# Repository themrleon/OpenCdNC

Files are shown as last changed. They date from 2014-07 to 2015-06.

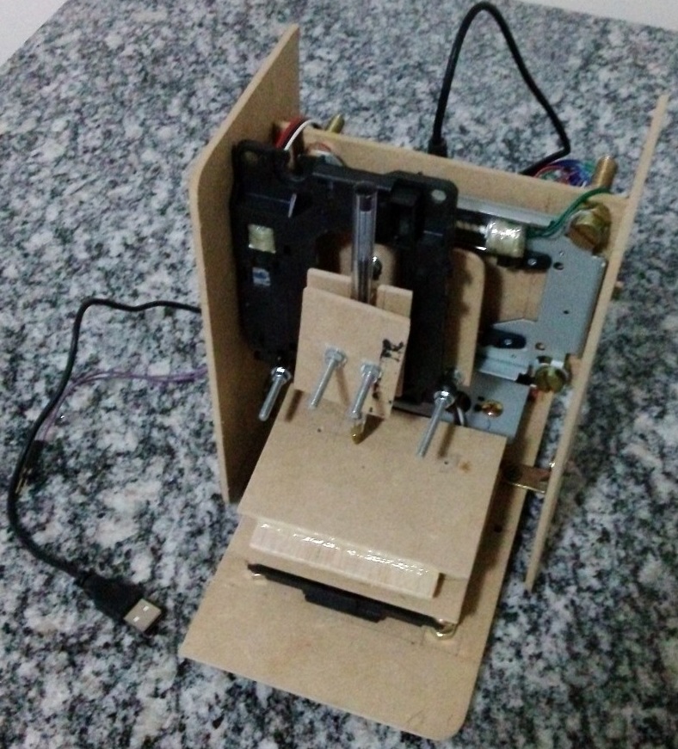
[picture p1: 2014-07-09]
Photos/full_off.jpg

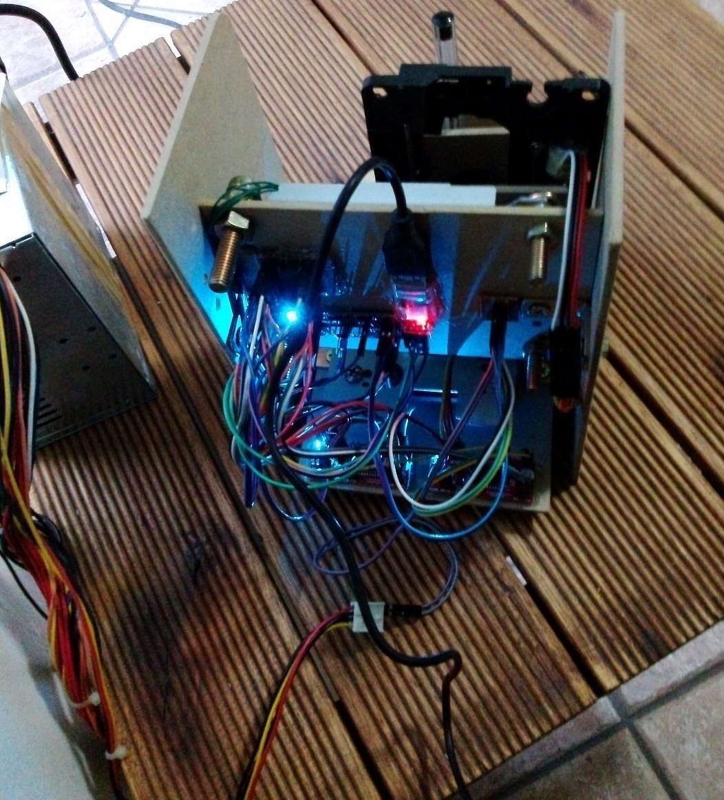
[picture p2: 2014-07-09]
Photos/back_on.jpg

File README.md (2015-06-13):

# OpenCdNC
<div align="justify">I always wanted a fast way to make PCB prototype before send the project to a fabhouse and wait 2 or more months to see the result. This is why I built this CNC, it's made from cd-rom parts and was inspired viewing some similar projects on internet.</div>

(https://www.youtube.com/watch?v=3wD8tHKAZS0)
(https://www.youtube.com/watch?v=hrWGD7YXcFc)

## Articles
* http://www.l3oc.com/2015/06/opencdnc-cnc-made-from-cdrom-parts.html
* http://hackaday.com/2014/07/09/cd-drive-cnc-machine-steals-matt-groenings-job-says-ha-ha/
* http://hackedgadgets.com/2014/07/15/opencdnc-cnc-project-made-from-cd-rom-drives/
* http://dangerousprototypes.com/2014/07/17/opencdnc-cnc-project-made-from-cd-rom-drives/
* http://www.geekweek.pl/aktualnosci/19815/maszyna-cnc-ze-starych-napedow-cd

## Features
* Cheap   - Just three cd-rom drives, wood, screws/bolts, cheap electronics, wires and any pen
* Compact - 20x15 cm of size and 35x38 mm of work area (varies from cd-rom), great for home use, small projects and SMDs
* Functional - Print over paper/copper to do circuit boards or just print images
* USB     - Native Windows/Linux USB driver support, no serial/parallel port or drivers needed
* Easy    - Just connect the USB cable to PC and supply the step motor driver with +5 VDC and GND
* Eagle   - Support one of the most popular PCB software design Cadsoft Eagle PCB (with limitations)
* Gerber  - Support GERBER RS274X protocol (with limitations)
* Precise - 0.147 mm virtual precision (varies from cd-rom motors, step motor driver, frame build quality...) 
* Code    - Small, clean and simple code. You can easily change/adapt to your own project

## What is used?
### Hardware
* 1x Microchip PIC16F628A
* 3x Easy Driver v4.4 Step Motor Driver
* 1x PL2303HX USB-Serial TTL Converter
* 3x CD-ROM Drives
* Some wood/screws for frame and wires for electronics

### Software
* Microsoft Windows 7
* Bloodshed Dev-C++ 4.9.9.2
* Microchip MPlab 8.92
* Hitech PICC Lite compiler
* Cadsoft Eagle PCB 6.6.0
* Microsoft Paint

## How the whole thing works?
### Protocol
`x00000y00000z1` - This is all what the firmware understand and need! Just send the X and Y coordinate in 'micrometer' unit and '1' or '2' for Z axis, where 1 = down and 2 = up.

### Software
<div align="justify">The software connect to CNC through a serial connection of 9600 kbps, send commands and wait the CNC process (move the motors), when done, CNC will return back a flag to software (an ASCII '*'), and then the software can send the next command.</div>

### Eagle
<div align="justify">The software was built to work with files generated by eagle CAM processor using the 'GERBER_RS274X' as device. The limitation here is in the gerber rs274x protocol, I added support just to 'wire' tool of Eagle toolbox, that generate these type of gerber commands:</div>
```
X000100Y000100D02*
X000100Y013874D01*
X013874Y013874D01*
X013081Y013908D02*
```
And what this mean? To print anything you will need use the 'wire' tool or import an image (see below).

## How to print images
<div align="justify">First step is convert the image to monochrome bitmap, this can be done with Microsoft Paint, you need reduce the image size too (something between 35x35 and 300x300 pixels would be ok, where less pixels = fast print and script draw time, but low quality). Then at Eagle you must use a script that import this bitmap file and draw the image using the 'wire' tool. The default Eagle's script name is 'import_bmp.ulp', but it draw the image with the 'rectangle' tool (that is useless to my software), so I modified it to draw using the 'wire' tool. Details in the tutorial folder.</div>

## License
See [LICENSE](https://github.com/themrleon/OpenCdNC/blob/master/LICENSE)

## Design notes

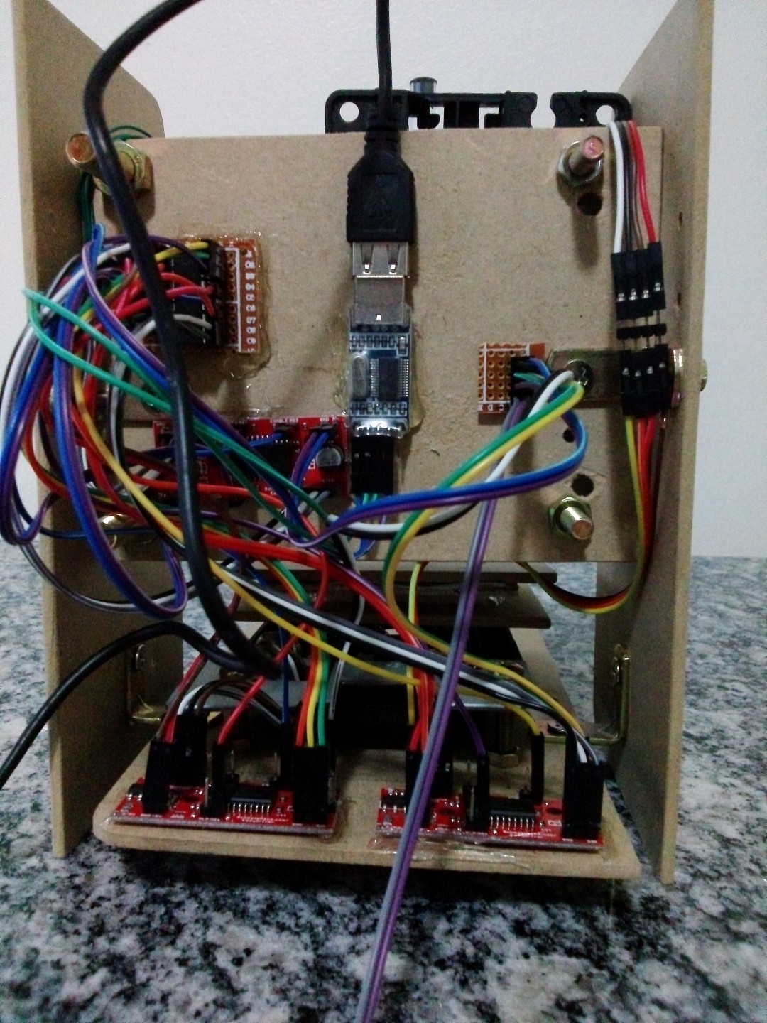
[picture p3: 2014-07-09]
Photos/back_close.jpg

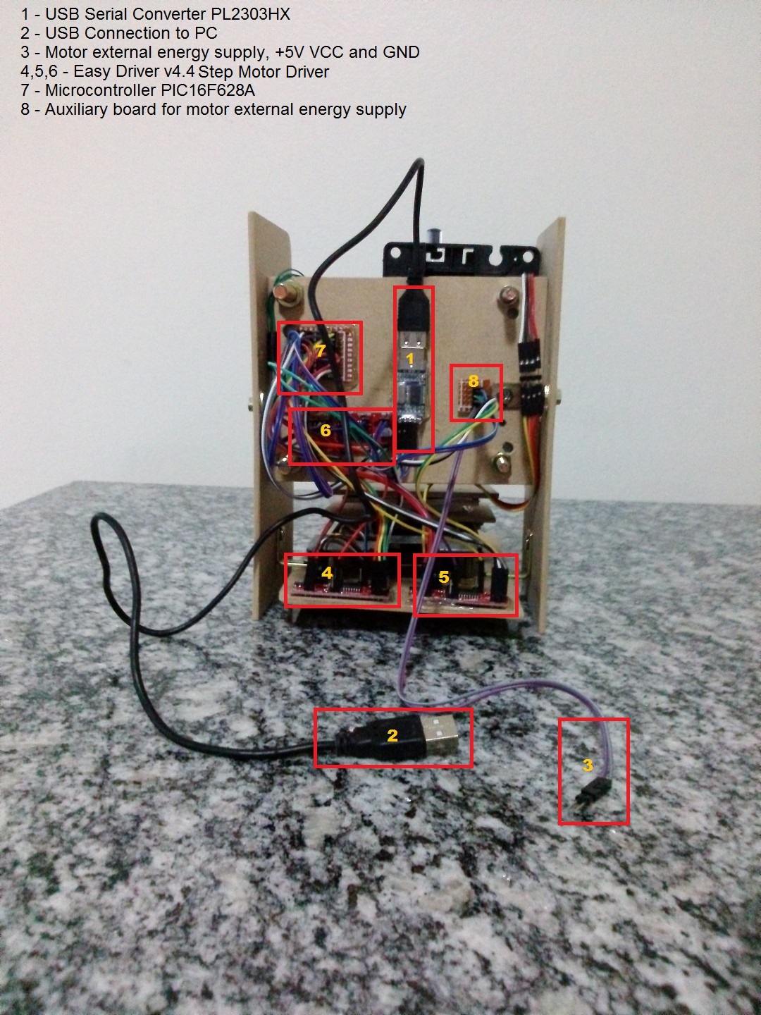
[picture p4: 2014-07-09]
Photos/back_full_detail.jpg

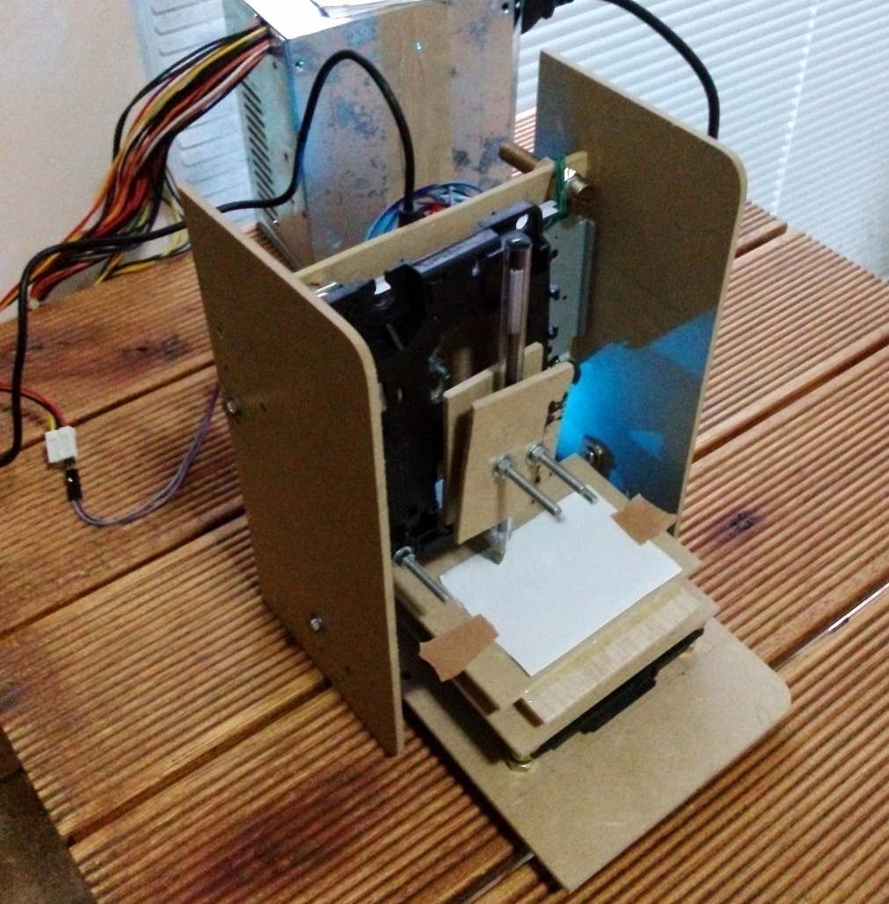
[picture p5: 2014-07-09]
Photos/full_on.jpg

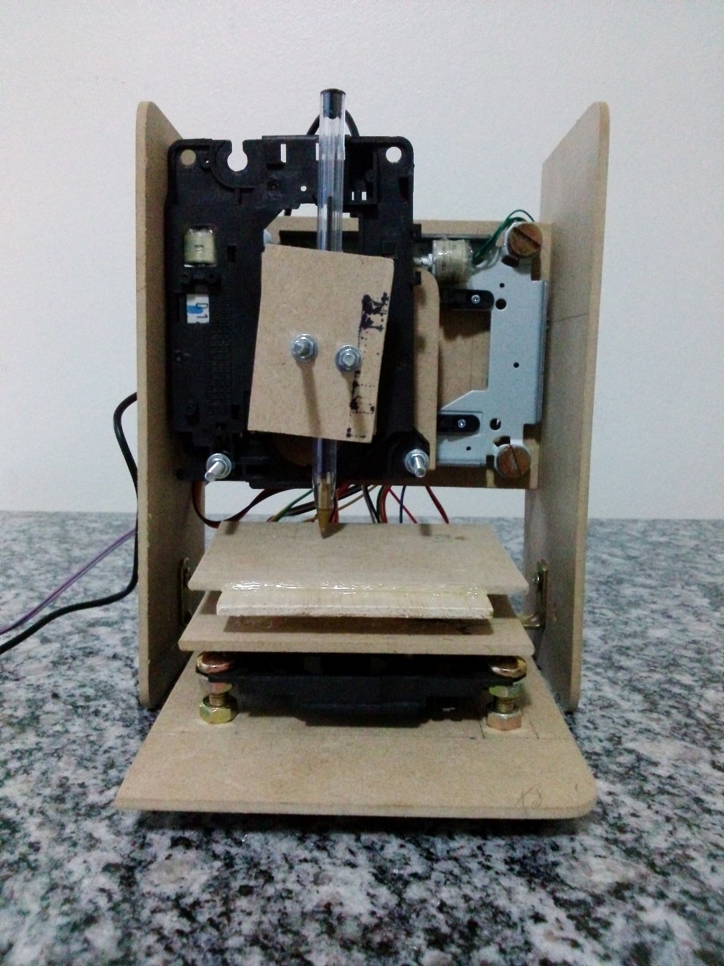
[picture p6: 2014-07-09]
Photos/reset_position.jpg

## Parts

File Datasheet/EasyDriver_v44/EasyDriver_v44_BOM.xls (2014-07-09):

EasyDriver V4.4 BOM
Qty | Ref | Description | Mfg Part Number | Disti part number | Distributor | Price @1 | Price @100 | Total Price @1 | Total Price @100
1 | IC1 | A3967 driver chip | A3967SLBTR-T | 59P3273 | Newark | 2.75 | 1.71 | 2.75 | 1.71
1 | C3 | CAP 47UF 35V ELECT MZA SMD | EMZA350ADA470MF61G | 565-2558-1-ND | DigiKey | 0.75 | 0.39 | 0.75 | 0.39
1 | C1 | CAP CER .10UF 50V Y5V 0603 | C1608Y5V1H104Z | 445-1324-1-ND | DigiKey | 0.04 | 0.02 | 0.04 | 0.02
2 | C4,C5 | CAP 680PF 50V CERAMIC X7R 0603 | CC0603KRX7R9BB681 | 311-1188-1-ND | DigiKey | 0.05 | 0.03 | 0.10 | 0.07
2 | R3,R4 | RES 20K OHM 1/10W 5% 0603 SMD | MCR03EZPJ203 | RHM20KGCT-ND | DigiKey | 0.07 | 0.02 | 0.14 | 0.04
2 | R1,R2 | RES .75 OHM 1/4W 1% 0805 SMD | MCR10EZHFLR750 | RHM.75MCT-ND | DigiKey | 0.14 | 0.10 | 0.28 | 0.20
1 | IC2 | IC REG ADJ 3-TERM SOT-223-4 | LM317MDCYR | 296-12631-1-ND | DigiKey | 0.80 | 0.45 | 0.80 | 0.45
1 | C2 | CAP 1UF 10V CER Y5V SMD 0603 | C0603C105Z8VACTU | 399-3216-1-ND | DigiKey | 0.04 | 0.03 | 0.04 | 0.03
1 | R16 | TRIMPOT 10K OHM 3MM CERMET SMD | TC33X-2-103E | TC33X-103ECT-ND | DigiKey | 0.20 | 0.14 | 0.20 | 0.14
1 | R5 | RES 5.1K OHM 1/10W 5% 0603 SMD | RC0603JR-075K1L | 311-5.1KGRCT-ND | DigiKey | 0.06 | 0.02 | 0.06 | 0.02
1 | PWR_LED | LED YELLOW 591NM 0603 SMD (2mA, 1.8V) | LY L29K-H1K2-26 | 475-1196-1-ND | DigiKey | 0.13 | 0.11 | 0.13 | 0.11
6 | R10,R11,R12,R13,R14,R15 | RES 10K OHM 1/10W 5% 0603 SMD | ERJ-3GEYJ103V | P10KGCT-ND | DigiKey | 0.07 | 0.02 | 0.43 | 0.13
1 | R9 | RES 1.0K OHM 1/10W 5% 0603 SMD | ERJ-3GEYJ102V | P1.0KGCT-ND | DigiKey | 0.07 | 0.02 | 0.07 | 0.02
1 | R8 | RES 240 OHM 1/10W 5% 0603 SMD | ERJ-3GEYJ241V | P240GCT-ND | DigiKey | 0.07 | 0.02 | 0.07 | 0.02
1 | R7 | RES 715 OHM 1/10W 1% 0603 SMD | ERJ-3EKF7150V | P715HCT-ND | DigiKey | 0.07 | 0.02 | 0.07 | 0.02
1 | R6 | RES 910 OHM 1/10W 5% 0603 SMD | ERJ-3GEYJ911V | P910GCT-ND | DigiKey | 0.07 | 0.02 | 0.07 | 0.02
1 | R17 | Do not populate at production | - | - | - | - | - | - | -
1 |  | PWB |  |  | Gold Phoenix | 1.00 | 1.00 | 1.00 | 1.00
 |  |  |  | Total |  |  |  | 7.01 | 4.41

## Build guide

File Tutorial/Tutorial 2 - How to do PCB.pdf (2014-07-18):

## OpenCdNC - How to do PCB

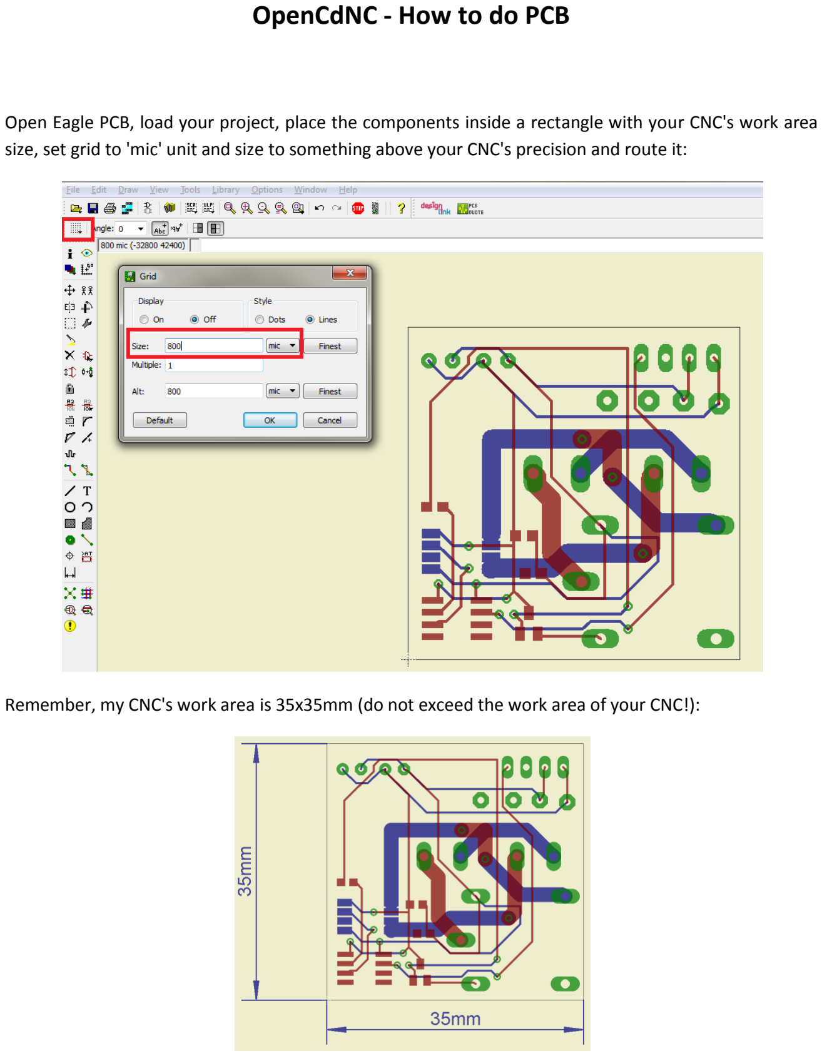
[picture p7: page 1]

Open Eagle PCB, load your project, place the components inside a rectangle with your CNC's work area size, set grid to 'mic' unit and size to something above your CNC's precision and route it:

Remember, my CNC's work area is 35x35mm (do not exceed the work area of your CNC!):

Let's print just vias, pads, dimension and top layer (choose from layer option):

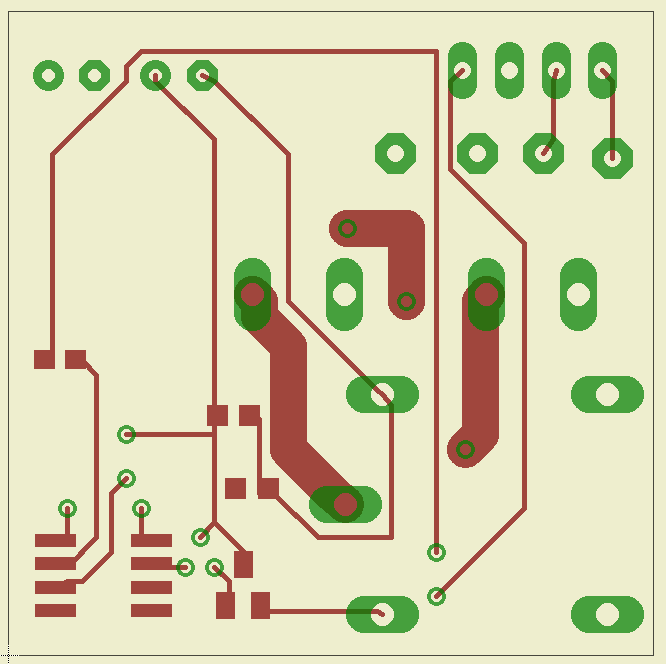
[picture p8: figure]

Now go to 'file'->'export'->'image', increase the resolution and set these checkbox:

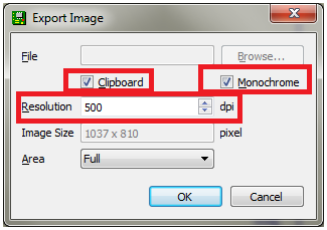
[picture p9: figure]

Now click 'ok', open MS Paint and paste:

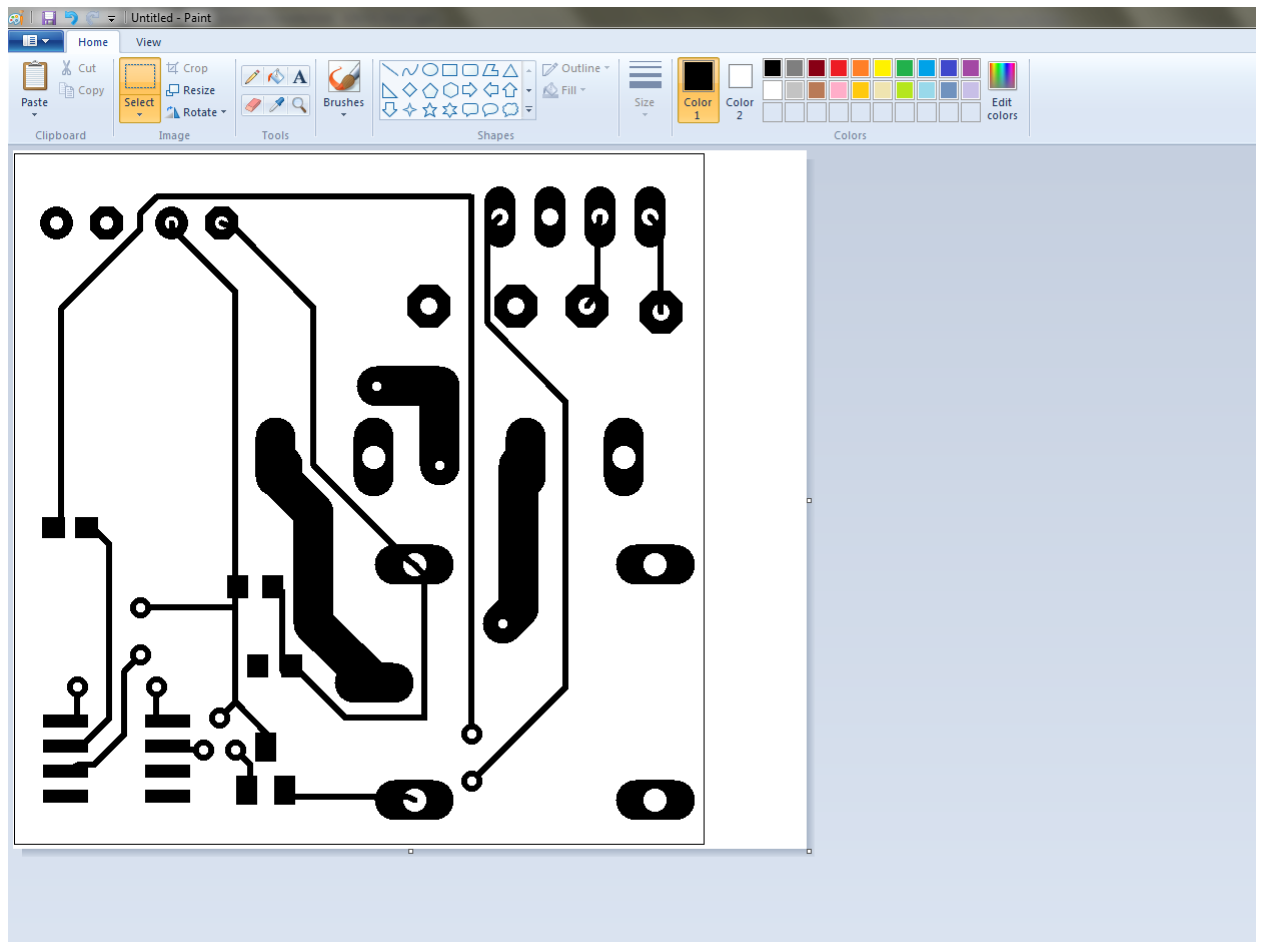
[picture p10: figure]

At this point we lost the reference of how many pixels is X mm, this is why we keep the work area rectangle around the board. As you remember from the 'how to print images' tutorial, we need reduce the image size to something lower than 300x300 pixels:

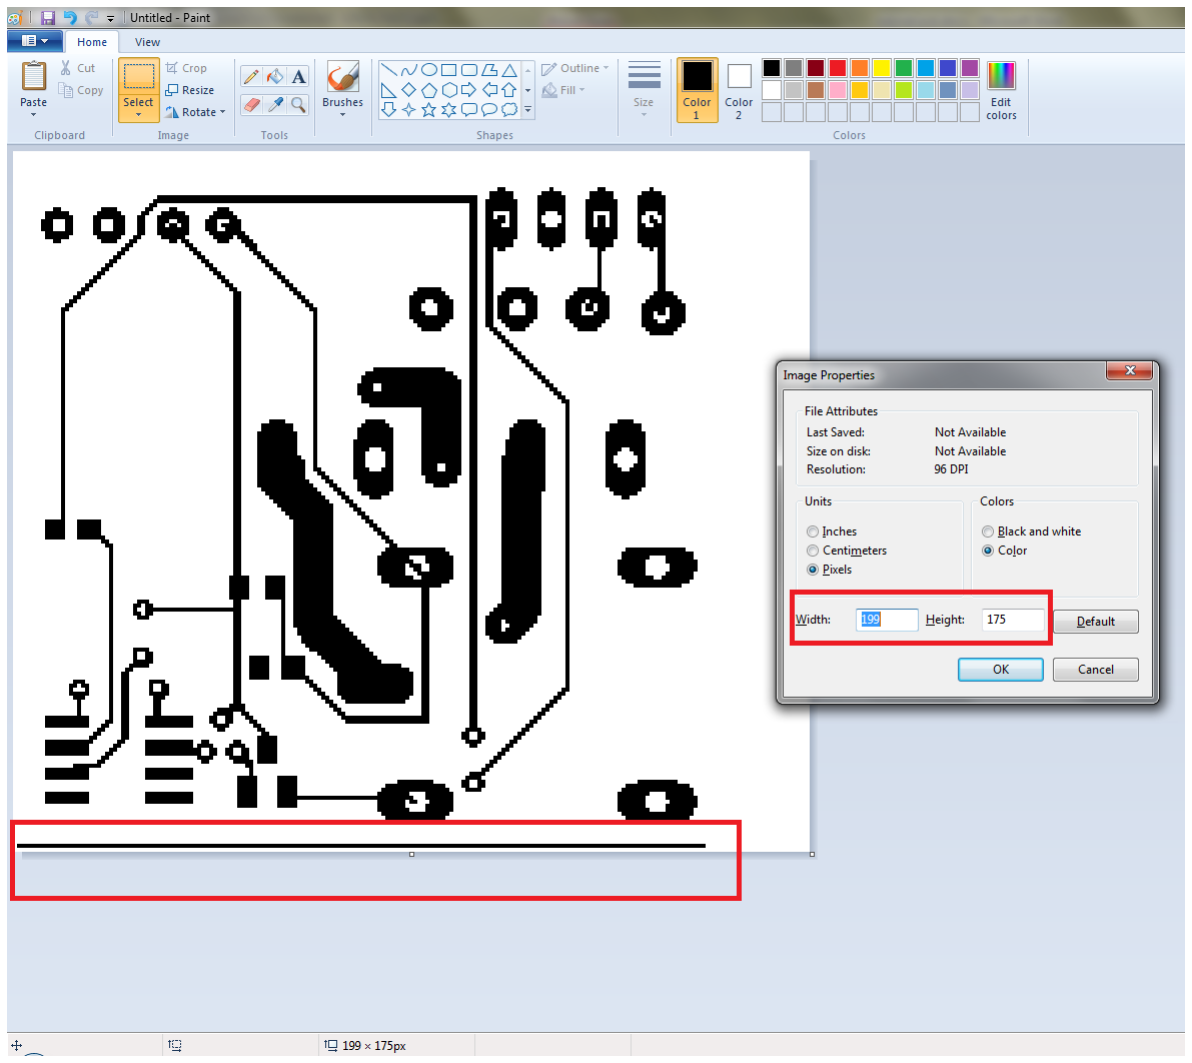
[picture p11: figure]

As we can see, the 35 mm horizontal reference still there, the image resolution was reduced to 199x175 pixels. Now resize the picture to fit exactly the horizontal/vertical reference dimension:

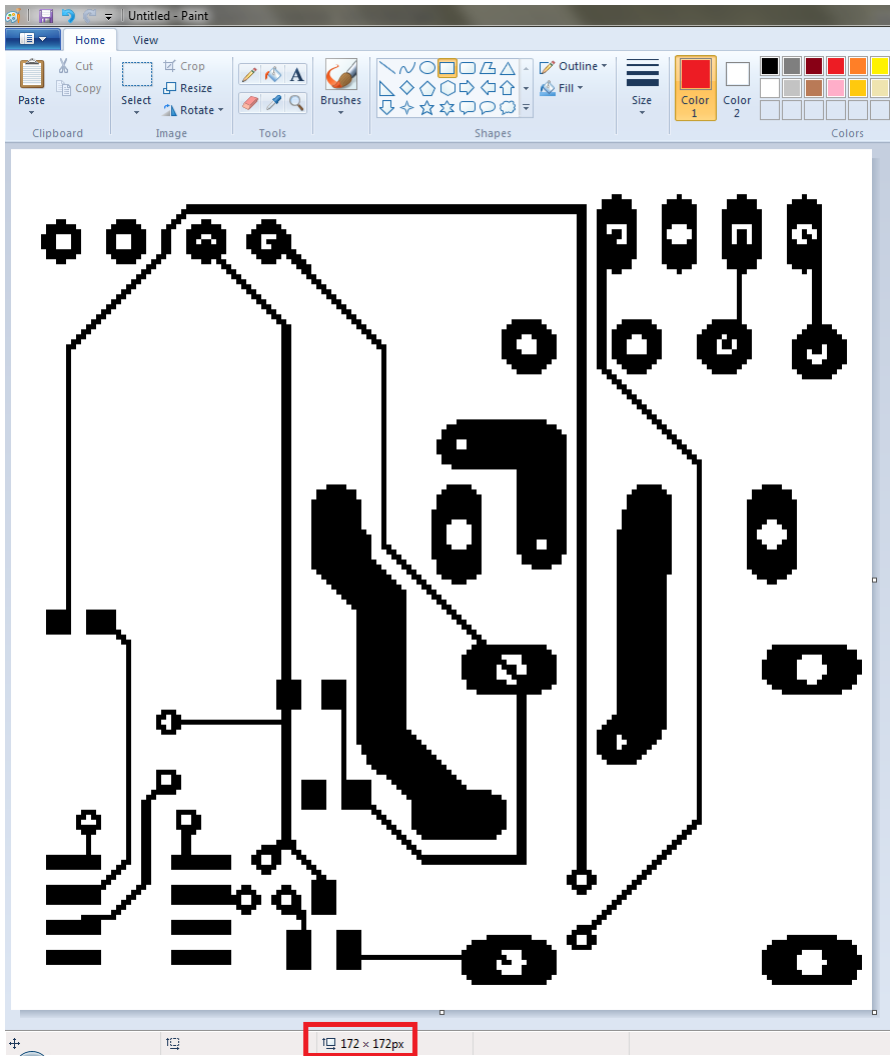
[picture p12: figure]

Now we have a 172x172 pixels image, just save as monochromatic bitmap, follow the 'How to print images' tutorial and you will have your board:

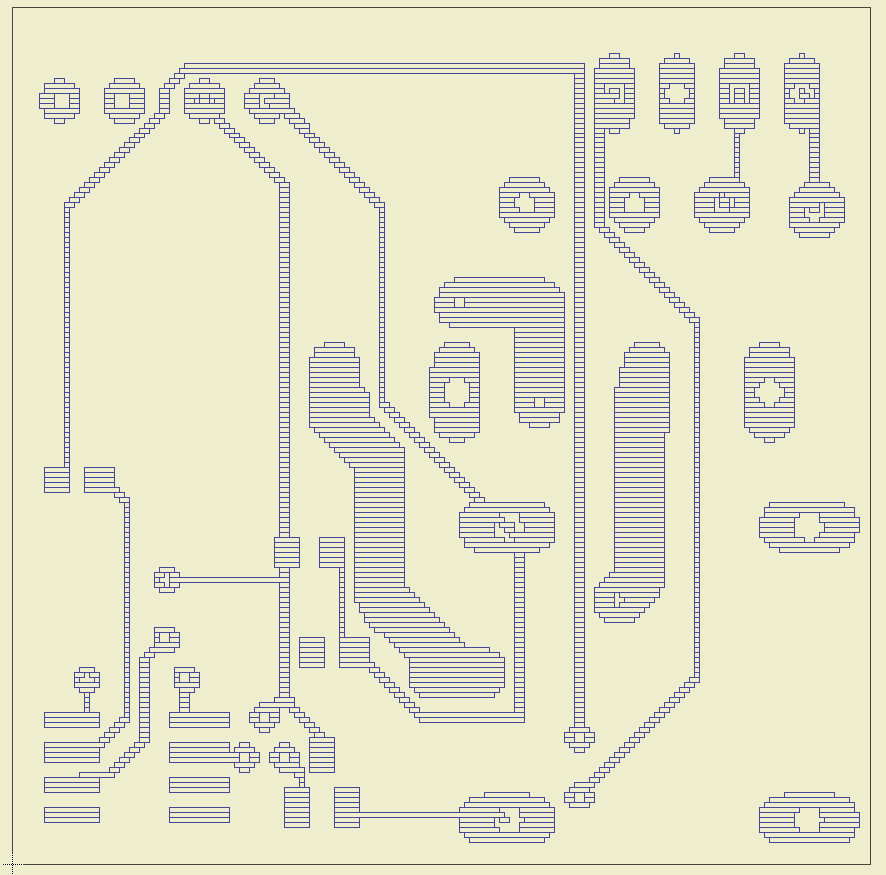
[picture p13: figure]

Due the CNC's precision, maybe you will have trouble at the distance between tracks, with experience and time you will know better your CNC's limitations and how to do a proper routing. Of course a really thin marker/pen and a solid CNC construction help a lot. You can use a laser module with a photoresist film too.

Another way to do PCB is using directly the 'wire' tool, then you can draw above the image layer (with horizontal and vertical lines manually), this will result in a faster and better print, because the pen/marker/laser will follow your wire just once, as a path, instead of draw the whole board with 'small rectangles'. After you print, just etch your board as usual!

https://github.com/themrleon/OpenCdNC

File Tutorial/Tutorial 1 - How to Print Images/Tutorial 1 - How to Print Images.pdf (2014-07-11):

## OpenCdNC - How to Print Images

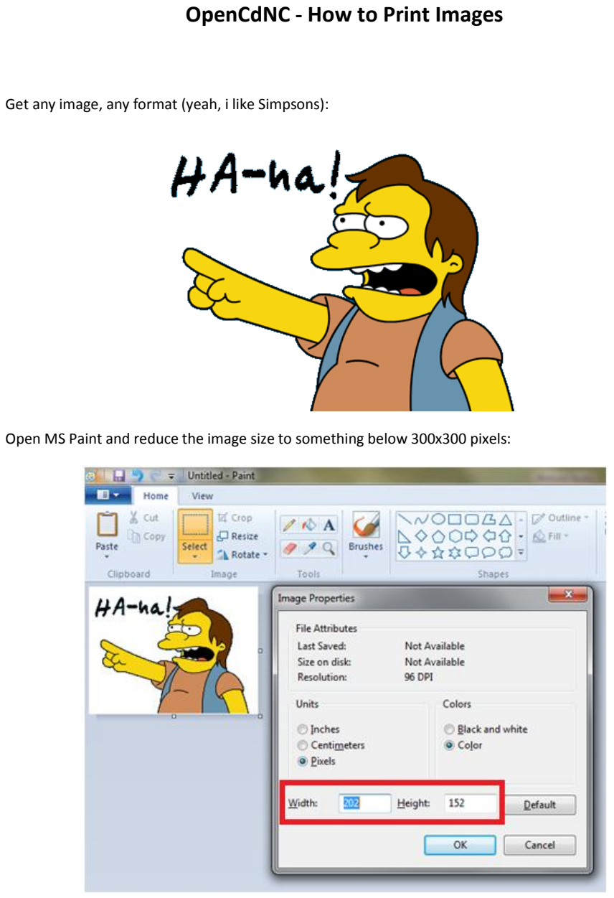
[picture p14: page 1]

Get any image, any format (yeah, i like Simpsons):

Open MS Paint and reduce the image size to something below 300x300 pixels:

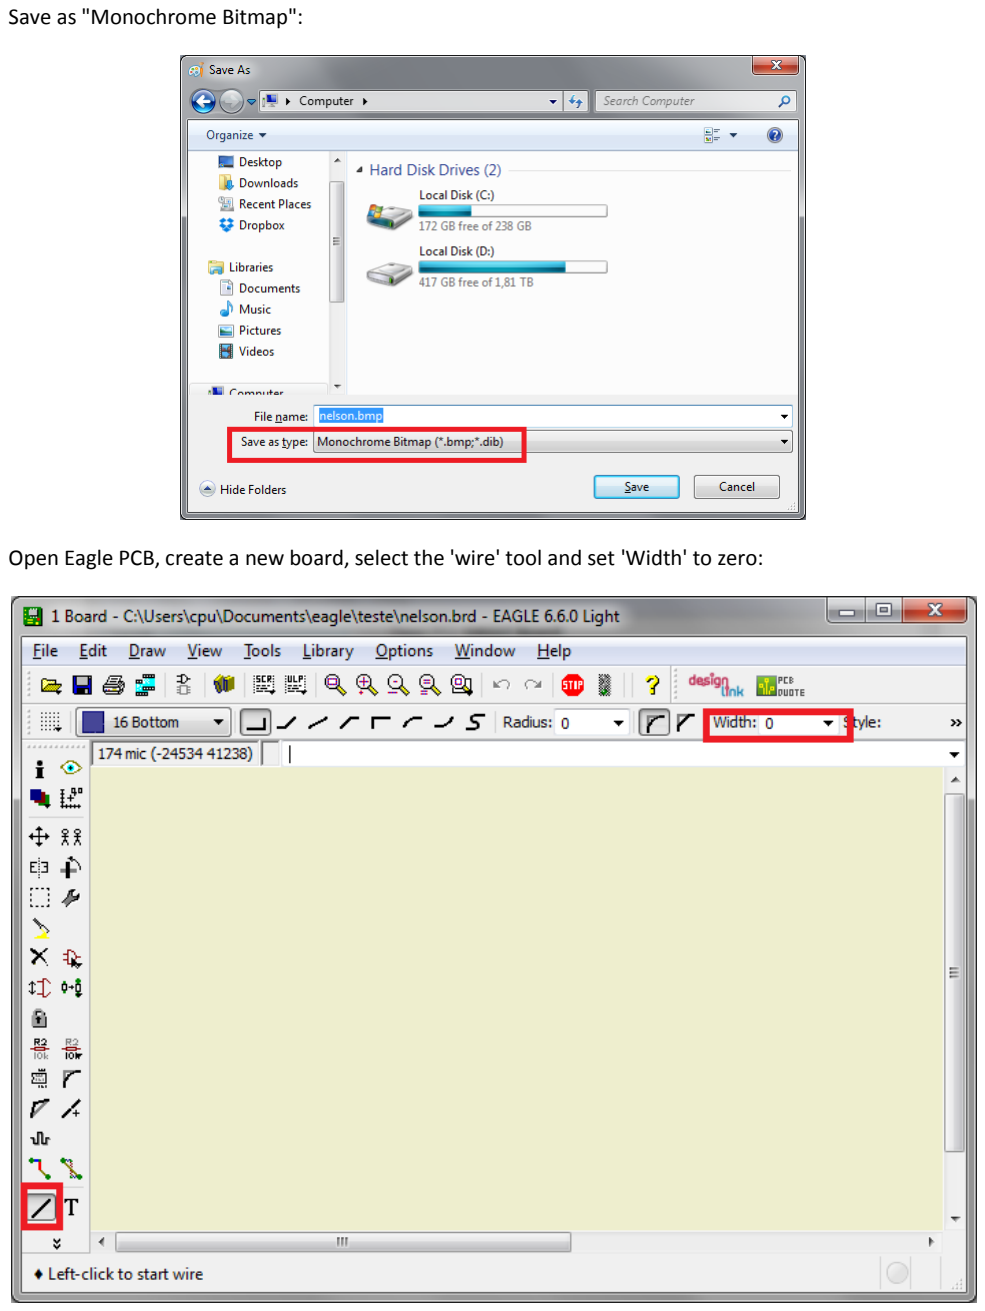
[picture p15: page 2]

Save as "Monochrome Bitmap":

Open Eagle PCB, create a new board, select the 'wire' tool and set 'Width' to zero:

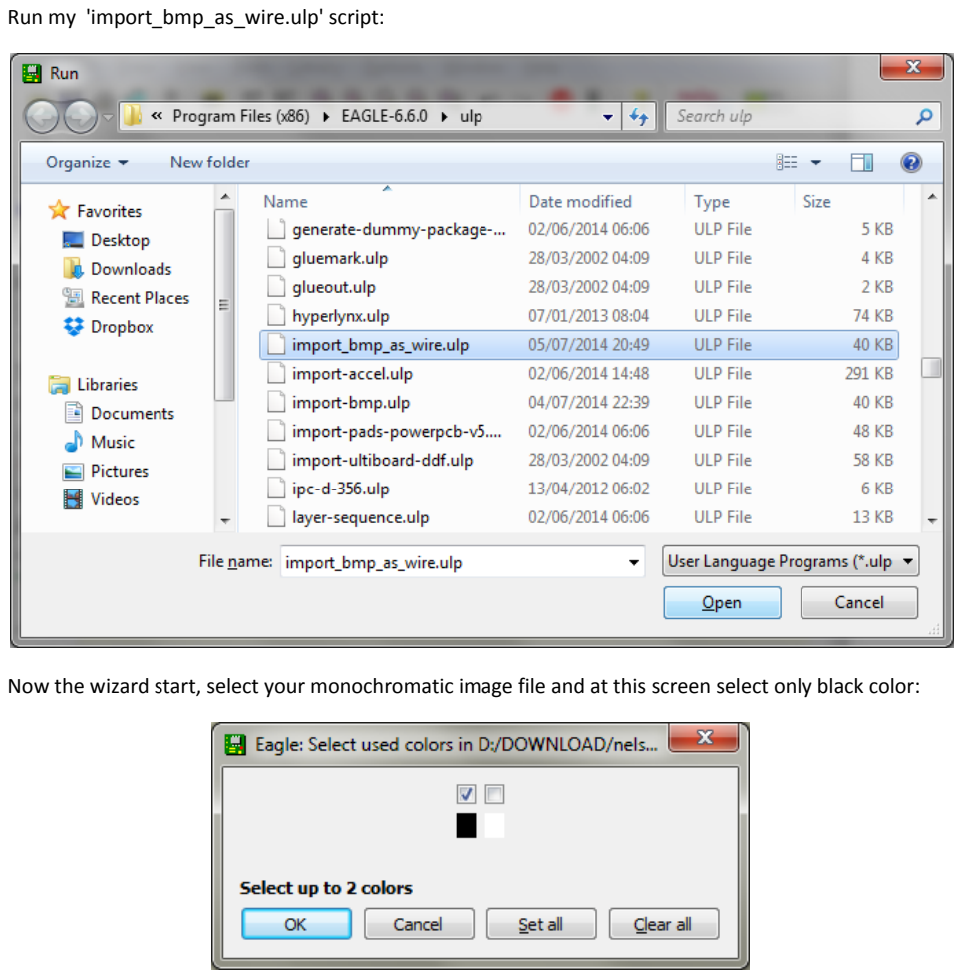
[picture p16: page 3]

Run my 'import_bmp_as_wire.ulp' script:

Now the wizard start, select your monochromatic image file and at this screen select only black color:

Now the math start and you will understand how and why the image size affect the whole thing (get a cup of tea):

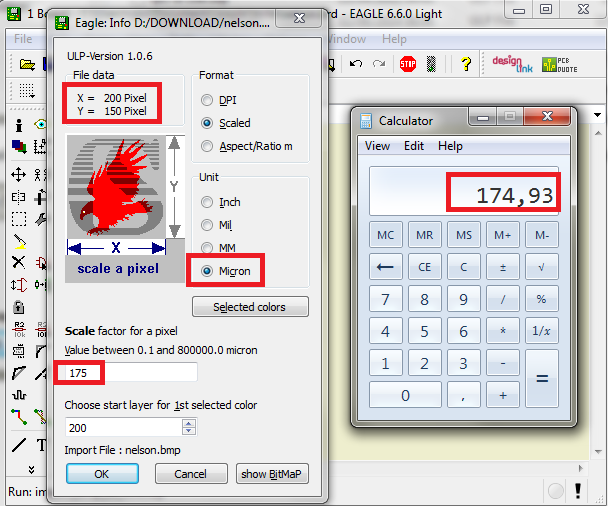
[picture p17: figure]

Remember, CNC's precision varies. MY CNC have 0.147 mm virtual precision, how i know? From the firmware code you will find "X_CM" and "Y_CM", that is how many steps you need to travel 1 cm. MY CNC need 68 steps to travel 1 cm on X axis, and 44 on Y axis (yeah, unfortunately i used 3 different brand cd rom drives, with different motors, consequently different precision, don't do this!).

Now only math, if 68 steps travel 1 cm = 10 mm, how many mm i travel with 1 step? 10/68=0,1470588235294118 mm = 147 micron! This is why MY CNC's precision will be different from YOURS.

Now you need know the work area of your CNC, mine have 38x35 mm, but lets use just 35x35 mm. If my precision is 147 micron, i can't draw something at 35000 micron position, but at 34986 micron yes, because my steps are of 147 micron, then 35000/147=238.0952380952381 and 238*147 = 34986 micron. Now do 34986/200 and you will get the 174.93 from image, 200 is the major dimension of the image, 200 pixels.

Now click 'ok' and you will get something like this:

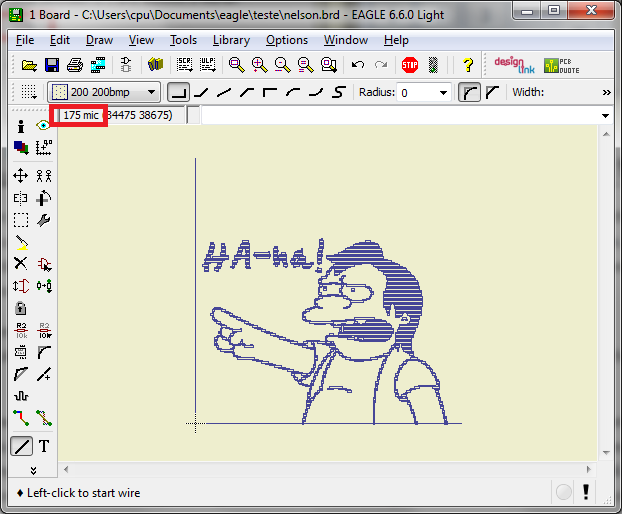
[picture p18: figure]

I like to place X and Y lines with the limits of my work area, as you can see, there are space left on Y axis due the 'irregular' image format (200x150), this is why a proportional image would fit better at the work area, like a 200x200 or 150x150.

If you give some zoom in, will see what the script did, many small rectagles, but with 'wire' tool :

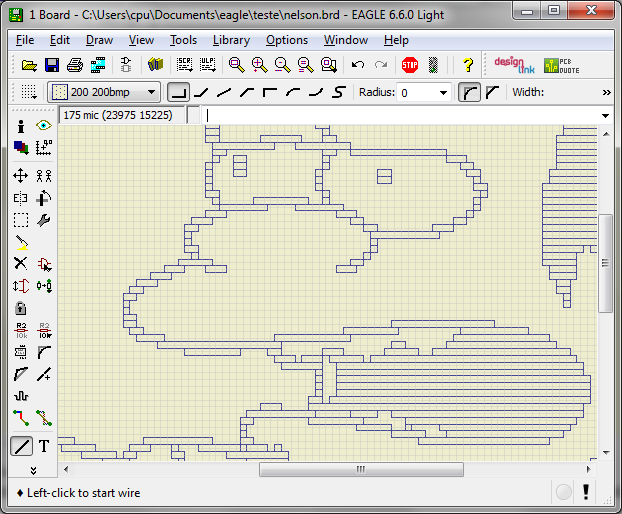
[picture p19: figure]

This is why you set the wire width to zero before run the script, otherwise, you can imagine what you would see at this point! madness!

Now at CAM Processor, select "GERBER_RS274X", set these checkbox and choose a name for the output file:

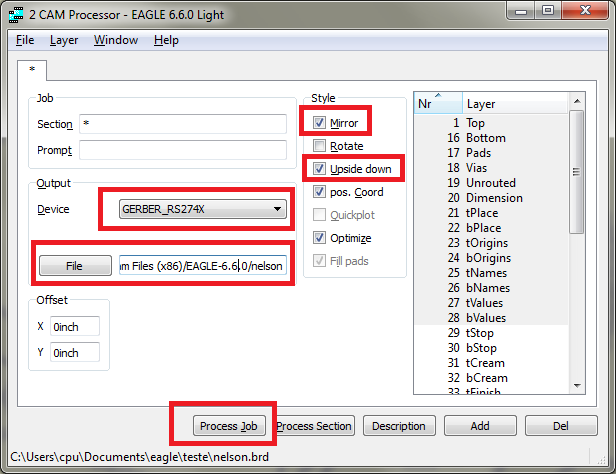
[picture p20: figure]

Click at 'Process Job' and wow! job complete! Now you can use this generated file as input for the Software.

All files used in this tutorial are available at the repository:

https://github.com/themrleon/OpenCdNC

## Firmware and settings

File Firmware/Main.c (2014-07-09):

/*The MIT License (MIT)

Copyright (c) 2014 Leonardo Ciocari

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
THE SOFTWARE IS PROVIDED "AS IS", WITHOUT WARRANTY OF ANY KIND, EXPRESS OR
IMPLIED, INCLUDING BUT NOT LIMITED TO THE WARRANTIES OF MERCHANTABILITY,
FITNESS FOR A PARTICULAR PURPOSE AND NONINFRINGEMENT. IN NO EVENT SHALL THE
AUTHORS OR COPYRIGHT HOLDERS BE LIABLE FOR ANY CLAIM, DAMAGES OR OTHER
LIABILITY, WHETHER IN AN ACTION OF CONTRACT, TORT OR OTHERWISE, ARISING FROM,
OUT OF OR IN CONNECTION WITH THE SOFTWARE OR THE USE OR OTHER DEALINGS IN THE
SOFTWARE.*/

//COMMAND EXAMPLES (With CNC at reset position "x00000y00000z1"):
//x00147y00147z1 - Invalid, can't move X and Y axis with Z down
//x00147y00147z2 - Valid, can move X and Y axis with Z up (will move X first, then Y)
//x00147y00000z1 - Valid, can move X to 00147 from actual 00000 position
//x00000y00294z1 - Valid, can move Y to 00294 from actual 00000 position

//CNC INFO
//Step motor driver at full step mode - each step = 0,147 mm = 147 mic

#include <htc.h>
#include <string.h>
#include <stdlib.h>

__CONFIG(INTIO & WDTDIS & MCLRDIS & BORDIS & LVPDIS);

#define _XTAL_FREQ 4000000

//Z Axis
#define Z_DIR	RB4	//1 - down, 0 - up
#define Z_STEP 	RB5
unsigned char Z_POS='1'; //'1' = down, '2' = up

//X Axis
#define X_DIR	RB0 //1 - left, 0 - right
#define X_STEP 	RA2	
#define X_CM	68	//Steps for 1 cm
unsigned int X_POS=0;	//Start at zero, upper left position

//Y Axis
#define Y_DIR	RA0	//1 - down, 0 - up
#define Y_STEP 	RA1
#define Y_CM	44	//Steps for 1 cm
unsigned int Y_POS=0;	//Start at zero, upper left position

//--------------------------------
void Xmove(unsigned int pos)
{
 unsigned int n,c;

 if(X_POS < pos)
  X_DIR=1;
 else
  X_DIR=0;

 //Get absolute value
 c=abs(pos-X_POS);

 for(n=0; n<c; n++)
 {
  X_STEP=1;
  __delay_ms(2);
  X_STEP=0;
  __delay_ms(2);

  if(X_DIR==1)
   X_POS++;
  else
   X_POS--;
 }
}

//--------------------------------
void Ymove(unsigned int pos)
{
 unsigned int n,c;

 if(Y_POS < pos)
  Y_DIR=1;
 else
  Y_DIR=0;

 //Get absolute value
 c=abs(pos-Y_POS);

 for(n=0; n<c; n++)
 {
  Y_STEP=1;
  __delay_ms(2);
  Y_STEP=0;
  __delay_ms(2);

  if(Y_DIR==1)
   Y_POS++;
  else
   Y_POS--;
 }
}

//--------------------------------
void Zmove(unsigned char pos)
{
 unsigned char n;

 if(Z_POS != pos)
 {
  if(pos == '1')
  {
   Z_DIR=1;
   Z_POS = '1';
  
   for(n=0; n<10; n++)
   {
    Z_STEP=1;
    __delay_ms(5);
    Z_STEP=0;
    __delay_ms(5);
   }
  }

  if(pos == '2')
  {
   Z_DIR=0;
   Z_POS = '2';
   
   for(n=0; n<10; n++)
   {
    Z_STEP=1;
    __delay_ms(5);
    Z_STEP=0;
    __delay_ms(5);
   }
  }
 }
}

//--------------------------------
void ScanUart()
{
 unsigned char x[6],y[6],z,tmp;
 unsigned int x_pos,y_pos;

 tmp=RCREG;
 
 if(tmp=='x')
 {
  //Get X
  while(RCIF!=1); x[0]=RCREG;
  while(RCIF!=1); x[1]=RCREG;
  while(RCIF!=1); x[2]=RCREG;
  while(RCIF!=1); x[3]=RCREG;
  while(RCIF!=1); x[4]=RCREG;

  //Get Y
  while(RCIF!=1); tmp=RCREG;
  while(RCIF!=1); y[0]=RCREG;
  while(RCIF!=1); y[1]=RCREG;
  while(RCIF!=1); y[2]=RCREG;
  while(RCIF!=1); y[3]=RCREG;
  while(RCIF!=1); y[4]=RCREG;

  //Get Z
  while(RCIF!=1); tmp=RCREG;
  while(RCIF!=1); z=RCREG;
 
  Zmove(z);	//First of X and Y, move Z axis

  //Convert from mic to steps
  x_pos=(atol(x)/(10000/X_CM));
  y_pos=(atol(y)/(10000/Y_CM));

  //If is a single axis move command (X or Y) move
  if( (X_POS == x_pos) || (Y_POS == y_pos) )
  {
   if( X_POS != x_pos )
    Xmove(x_pos);

   if( Y_POS != y_pos )
    Ymove(y_pos);
  }
  else if(z == '2') //else is a two axis move command, but only move if Z axis is up
  {
   Xmove(x_pos);	//First X then Y
   Ymove(y_pos);
  }

  while(TXIF!=1); TXREG='*';	//After execute command succesful, send back to software a flag '*'
 }
}

//---------------------------------------------------
int main()
{
 TRISA=0b00000000;

 //PORTB
 RBPU=0;	//Pull-up on
 TRISB=0b00000010;
 PORTB=0b00000000;

 //Turn off analog comparator
 CM2=1;
 CM1=1;
 CM0=1;

 //USART
 BRGH=1;	//High Speed
 SPBRG=25;	//9600 at 4Mhz
 SYNC=0;
 SPEN=1;	//USART enabled
 TXEN=1;
 CREN=1;
 
 //Wait 1 second (circuit stabilization)
 __delay_ms(250);
 __delay_ms(250);
 __delay_ms(250);
 __delay_ms(250);

 X_DIR=0;
 Y_DIR=0;
 Z_DIR=1;
 
 X_STEP=0;
 Y_STEP=0;
 Z_STEP=0;

 Y_POS=0;
 X_POS=0;
 Z_POS='1';

 while(10)
 {
  if(OERR==1)	//Avoid serial overflow hangs
  {
   CREN=0;
   CREN=1;
  }

  if(RCIF==1)	//Wait serial receive something
   ScanUart();
 }

}

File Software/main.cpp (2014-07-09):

/*The MIT License (MIT)

Copyright (c) 2014 Leonardo Ciocari

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
THE SOFTWARE IS PROVIDED "AS IS", WITHOUT WARRANTY OF ANY KIND, EXPRESS OR
IMPLIED, INCLUDING BUT NOT LIMITED TO THE WARRANTIES OF MERCHANTABILITY,
FITNESS FOR A PARTICULAR PURPOSE AND NONINFRINGEMENT. IN NO EVENT SHALL THE
AUTHORS OR COPYRIGHT HOLDERS BE LIABLE FOR ANY CLAIM, DAMAGES OR OTHER
LIABILITY, WHETHER IN AN ACTION OF CONTRACT, TORT OR OTHERWISE, ARISING FROM,
OUT OF OR IN CONNECTION WITH THE SOFTWARE OR THE USE OR OTHER DEALINGS IN THE
SOFTWARE.*/

#include <windows.h>
#include <stdio.h>
#include <string.h>
#include <conio.h>
#include <math.h>
#include <iostream>
#include <sstream>
#include <string> 

using namespace std;
HANDLE hPort;

//--------------------------------------------------------- 
BOOL WriteByte(BYTE bybyte)
{
    DWORD iBytesWritten=0;
    DWORD iBytesToRead = 1;
    if(WriteFile(hPort,(LPCVOID)
        &bybyte,iBytesToRead,&iBytesWritten,NULL)==0)
        return FALSE;
    else return TRUE;
}

//--------------------------------------------------------- 
BOOL WriteString(const void *instring, int length)
{
    int index;
    BYTE *inbyte = (BYTE *) instring;
    for(index = 0; index< length; ++index)
    {
        if (WriteByte(inbyte[index]) == FALSE)
            return FALSE;
    }
    return TRUE;
}

//--------------------------------------------------------- 
BOOL ReadByte(BYTE  &resp)
{
    BOOL bReturn = TRUE;
    BYTE rx;
    DWORD dwBytesTransferred=0;
 
    if (ReadFile (hPort, &rx, 1, &dwBytesTransferred, 0)> 0)
    {
        if (dwBytesTransferred == 1)
        {
            resp=rx;
            bReturn  = TRUE;
        }
        else bReturn = FALSE;
    }
    else    bReturn = FALSE;
    return bReturn;
}

//--------------------------------------------------------- 
void ClosePort()
{
    CloseHandle(hPort);
    return;
}

//---------------------------------------------------------
HANDLE ConfigureSerialPort(LPCSTR  lpszPortName)
{
    HANDLE hComm = NULL;
    DWORD dwError;
    DCB PortDCB;
    COMMTIMEOUTS CommTimeouts;
    // Open the serial port.
    hComm = CreateFile (lpszPortName, // Pointer to the name of the port
        GENERIC_READ | GENERIC_WRITE,
        // Access (read-write) mode
        0,              // Share mode
        NULL,           // Pointer to the security attribute
        OPEN_EXISTING,  // How to open the serial port
        0,              // Port attributes
        NULL);          // Handle to port with attribute
    // to copy
 
    // Initialize the DCBlength member.
    PortDCB.DCBlength = sizeof (DCB);
    // Get the default port setting information.
    GetCommState (hComm, &PortDCB);
    // Change the DCB structure settings.
    PortDCB.BaudRate = 9600;              // Current baud
    PortDCB.fBinary = TRUE;               // Binary mode; no EOF check
    PortDCB.fParity = TRUE;               // Enable parity checking
    PortDCB.fOutxCtsFlow = FALSE;         // No CTS output flow control
    PortDCB.fOutxDsrFlow = FALSE;         // No DSR output flow control
    PortDCB.fDtrControl = DTR_CONTROL_ENABLE;
    // DTR flow control type
    PortDCB.fDsrSensitivity = FALSE;      // DSR sensitivity
    PortDCB.fTXContinueOnXoff = TRUE;     // XOFF continues Tx
    PortDCB.fOutX = FALSE;                // No XON/XOFF out flow control
    PortDCB.fInX = FALSE;                 // No XON/XOFF in flow control
    PortDCB.fErrorChar = FALSE;           // Disable error replacement
    PortDCB.fNull = FALSE;                // Disable null stripping
    PortDCB.fRtsControl = RTS_CONTROL_ENABLE;
    // RTS flow control
    PortDCB.fAbortOnError = FALSE;        // Do not abort reads/writes on
    // error
    PortDCB.ByteSize = 8;                 // Number of bits/byte, 4-8
    PortDCB.Parity = NOPARITY;            // 0-4=no,odd,even,mark,space
    PortDCB.StopBits = ONESTOPBIT;        // 0,1,2 = 1, 1.5, 2
 
    // Configure the port according to the specifications of the DCB
    // structure.
    if (!SetCommState (hComm, &PortDCB))
    {
        printf("Could not configure serial port\n");
        return NULL;
    }
    // Retrieve the time-out parameters for all read and write operations
    // on the port.
    GetCommTimeouts (hComm, &CommTimeouts);
    // Change the COMMTIMEOUTS structure settings.
    CommTimeouts.ReadIntervalTimeout = MAXDWORD;
    CommTimeouts.ReadTotalTimeoutMultiplier = 0;
    CommTimeouts.ReadTotalTimeoutConstant = 0;
    CommTimeouts.WriteTotalTimeoutMultiplier = 0;
    CommTimeouts.WriteTotalTimeoutConstant = 0;
    if (!SetCommTimeouts (hComm, &CommTimeouts))
    {
        printf("Could not set timeouts\n");
        return NULL;
    }
    return hComm;
}

//---------------------------------------------------------
int main(void)
{   
    unsigned int x_offset,y_offset;
    char out[20]="",tmp[20]="";
    BYTE rx;
    
    ClosePort();
    hPort = ConfigureSerialPort("COM5");

    if(hPort == NULL)
     printf("Com port configuration failed\n");
    else
    {
     FILE *f = fopen("nelson","rb");
     char in[20];
     
     while(fgets(in,50,f)!=NULL)
     {
      if(in[0]=='X')
      {
       //Get X value
       printf("\n\nIN - %s",in); 
       memcpy( tmp, &in[1], 6 );
       tmp[6] = '\0';
       unsigned int x = atol(tmp);
       sprintf(tmp, "%5.0f", x*2.54);
       strcpy(out,"x");
       strcat(out,tmp);
       
       //Get Y value
       memcpy( tmp, &in[8], 6 );
       tmp[6] = '\0';
       unsigned int y = atol(tmp);
       sprintf(tmp, "%5.0f", y*2.54);
       strcat(out,"y");
       strcat(out,tmp);
       
       //Get Z value
       memcpy( tmp, &in[16], 1 );
       tmp[1] = '\0';
       strcat(out,"z");
       strcat(out,tmp);
       
       //Replace ' ' with '0'
       for(int a=0;a<strlen(out);a++)
       {
        if(out[a]==' ')
         out[a]='0';        
       }
       
       //Out to CNC
       printf("OUT=%s",out);
       WriteString(out,strlen(out));
       while(rx!='*')
        ReadByte(rx);
       rx=0;
      }
     }//while
     
     //Last command to CNC, reset position
     WriteString("x00000y00000z2",14);
     while(rx!='*')
      ReadByte(rx);
     rx=0;

     ClosePort();
    }
   
    printf("\n");
    system("pause");
    return 0;
}

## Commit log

2014-07-10 Added tutorial
    [nelson.brd]
2014-07-18 Added How to do PCB tutorial
    [nelson.brd]
2014-07-19 Update tutorial
    [nelson.brd]
